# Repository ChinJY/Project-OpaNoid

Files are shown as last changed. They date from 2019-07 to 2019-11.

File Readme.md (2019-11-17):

## Project OpaNoid

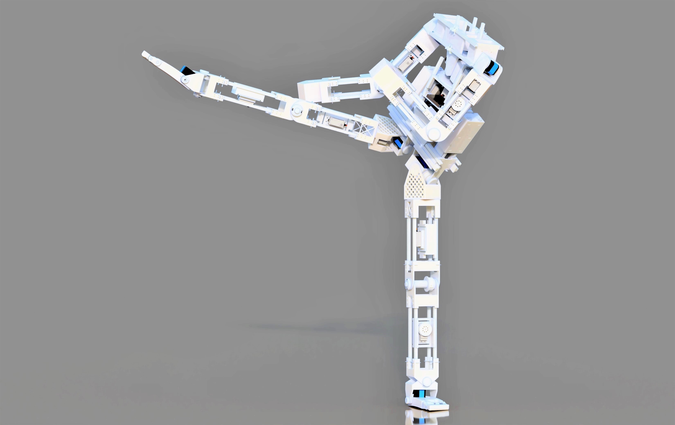
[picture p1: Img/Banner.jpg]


-   Project OpaNoid is an teen to adult-sized humanoid robot designed
    for education and research. It is highly modular
    and can be modified on the fly using only simple tools such as hex-head
    screwdrivers.

-   Its chassis has been designed to be completely printed with using FDM
    3D printing (the most accessible 3D printing technique at present)

-   By focusing on the humanoid form, greater attention can be paid to the key
    objectives of Project Opanoid; namely its variable mass distribution,
    variable dimensions, scalability (servos can be stacked to support higher
    torque requirements) and expandability (add-ons such as sensors can be added
    without modification to the core structure through the use of
    rail-mountings)

### Open Source

Project OpaNoid is open source under Creative Commons BY-SA 4.0 for hardware and GNU GPL v3 for software.

### Getting started

-   [Bill of materials](Hardware/Bill%20of%20materials.pdf)

-   [Printing guidelines](Hardware/Print%20settings.md)

-   [Software setup](Software/Software%20readme.md)

-   [Contribution Guidelines](Contributor%20guidelines.md)

-   [Codes of conduct](Codes%20of%20conduct.md)

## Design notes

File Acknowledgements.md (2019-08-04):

3216HTG servo: <https://grabcad.com/library/ars-3216htg-hv-1>

Turnigy S901D: <https://grabcad.com/library/turnigy-tgy-s901d-digital-servo-1>

9-axis imu:  <https://grabcad.com/library/adafruit-9-dof-imu-breakout-1>

pi camera: 
<https://grabcad.com/library/raspberry-pi-camera-module-v2-1/details?folder_id=4151951>

ultrasonic rangefinder: 
<https://grabcad.com/library/ultrasonic-sensor-hc-sr04-1>

LiPo battery:  <https://grabcad.com/library/lipo-battery-1-1>

AX-12A:  <https://grabcad.com/library/servo-dynamixel-ax-12a-1>

CR-10S: 
<https://grabcad.com/library/modified-creality-cr-10s-s3-model-3d-printer-assembly-1>

DQN template:
<https://github.com/sezan92/self_balancing_robot>

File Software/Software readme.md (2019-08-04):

-   Refer to this page to install Pigpio on Raspberry
    Pi: <http://abyz.me.uk/rpi/pigpio/download.html>

-   Install VNC solution (e.g. VNC viewer)

-   *Generate motion capture logs using Kinect on PC*

    -   Install kinect
        sdk: <https://www.microsoft.com/en-us/download/details.aspx?id=44561>

    -   Open ```BodyBasics-WPF.sln``` in Microsoft Visual Studio and run it
    
    -   Copy and paste the console output into an empty plain text file
    
    -   Delete all non-numerical items from the output in the beginning and the end, and save it as a text file to generate the motion capture log

        -   Please note that toe motions are not supported by
            kinect, so an additional capture device would be required
    
    -   Copy the motion capture log into ```Software/project_opanoid/walk_data```

-   *Controller program on raspberry pi*

    -   Save ```Software/Raspberry Pi/Opanoid_controller.c``` into your robot's Raspberry Pi 

    -   On your Raspberry Pi, copy the desired motion capture logs from ```Software/project_opanoid/walk_data``` to the same folder as the controller program

    -   Replace the path in line 29 of the controller program to the that of the motion capture log

    -   Run the controller program to make OpaNoid move in accordance with the motion capture log
    
-   *ROS package*

    -   Copy the ```project_opanoid``` folder into the source folder of your ROS workspace
        
    -   In Terminal, cd to your ROS workspace
    
    -   Type ```source devel/setup.bash``` (source the workspace)
    
    -   Enter different commands to open various functions:
    
        -   ```roslaunch project_opanoid display.launch``` to view the model of OpaNoid in Rviz
        
        -   ```roslaunch project_opanoid world.launch``` to view the model of OpaNoid in a Gazebo simulation
        
             -   Open another tab, go to the root folder of your ROS workspace,  source it and type ```rosrun project_opanoid_project_opanoid_node``` to move the robot using motion capture logs located in the Software/project_opanoid/walk_data folder
             
                 -   Change the file path in ```Software/project_opanoid/src/walk.cpp```, line 15 to that of your movement log in order to play it
                 
        -   ```roslaunch project_opanoid main_DQN.launch``` to make OpaNoid walk in Gazebo using a Deep Q Network Controller (not working at the moment)
    
    -   You can alter the simulated robot robot at ```Software/project_opanoid/urdf/opanoid_full.urdf```

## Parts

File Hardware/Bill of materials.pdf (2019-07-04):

## Bill of materials

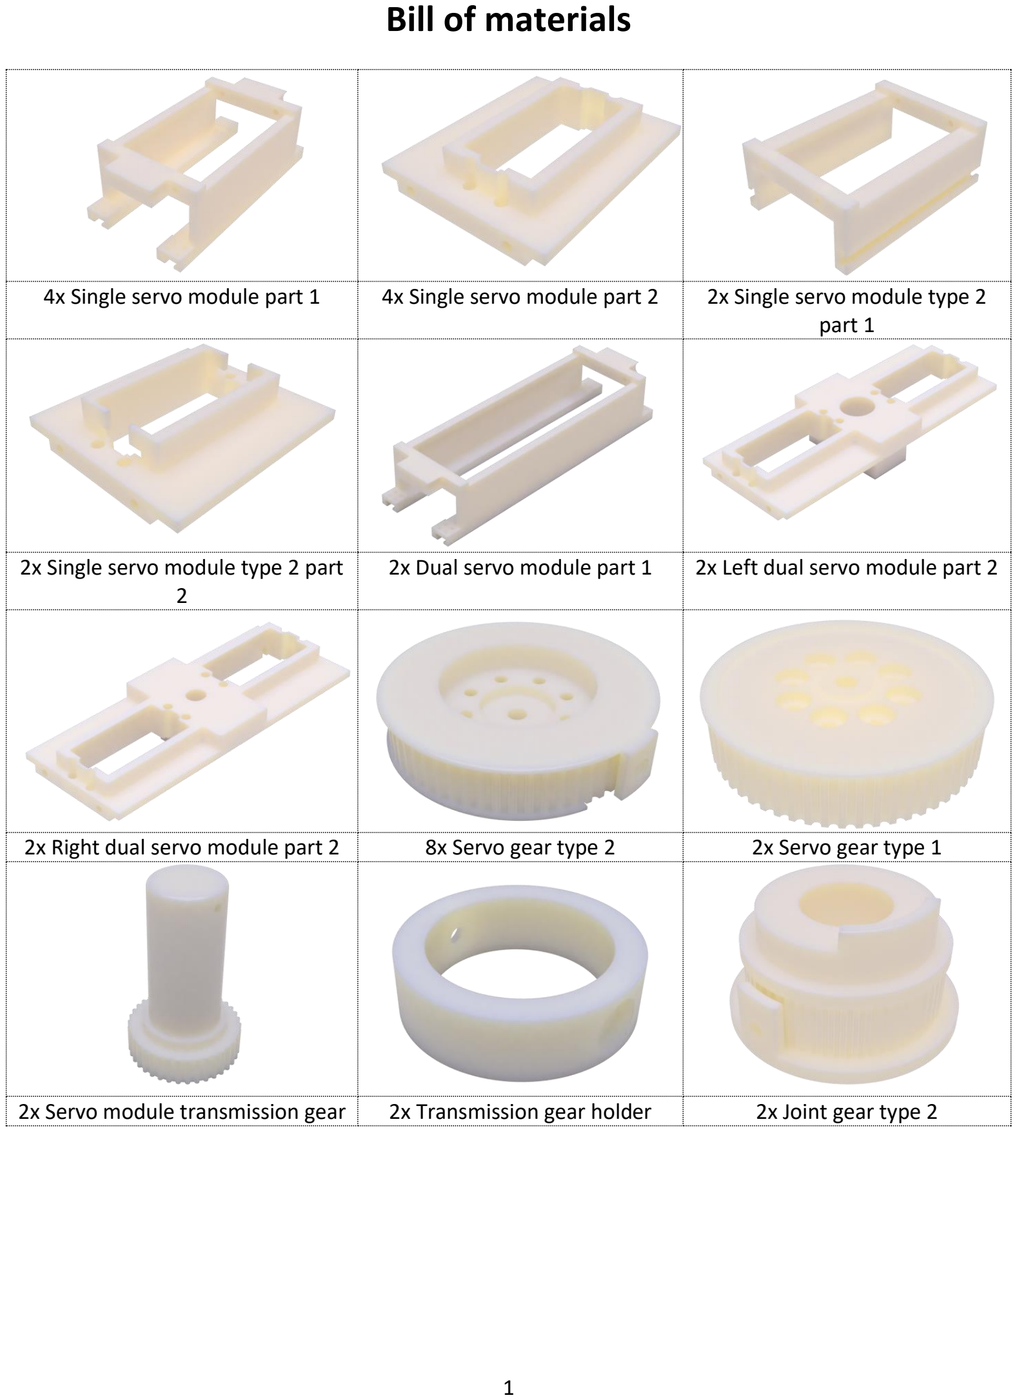
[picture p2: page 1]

4x Single servo module part 1 | 4x Single servo module part 2 | 2x Single servo module type 2 part 1

2x Single servo module type 2 part 2

2x Dual servo module part 1 | 2x Left dual servo module part 2
2x Right dual servo module part 2 | 8x Servo gear type 2 | 2x Servo gear type 1
2x Servo module transmission gear | 2x Transmission gear holder | 2x Joint gear type 2

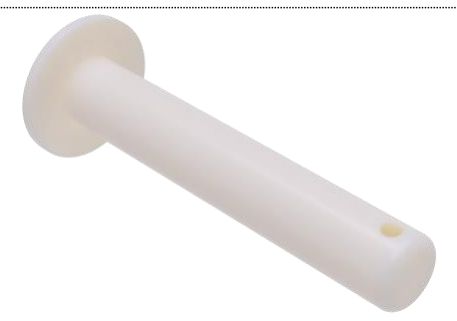
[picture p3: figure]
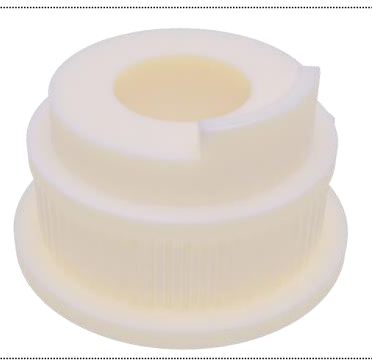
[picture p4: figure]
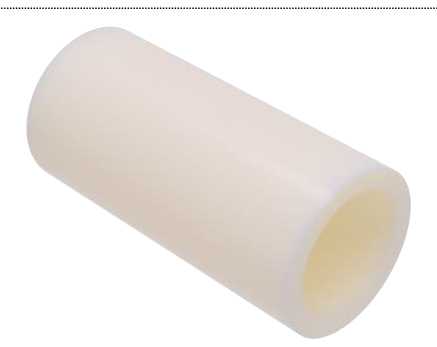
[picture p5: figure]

2x Joint gear type 2 | 4x Joint pin | 4x Joint spacer

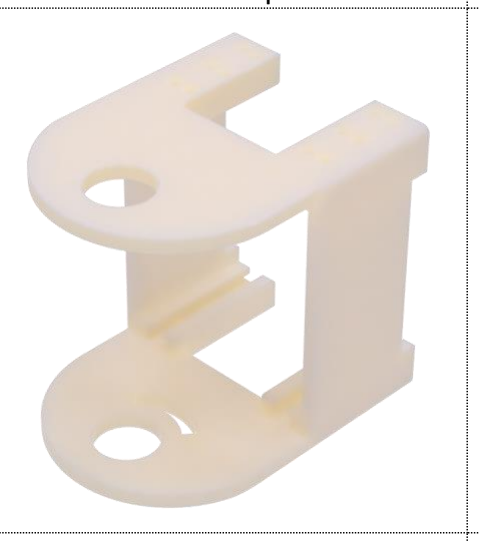
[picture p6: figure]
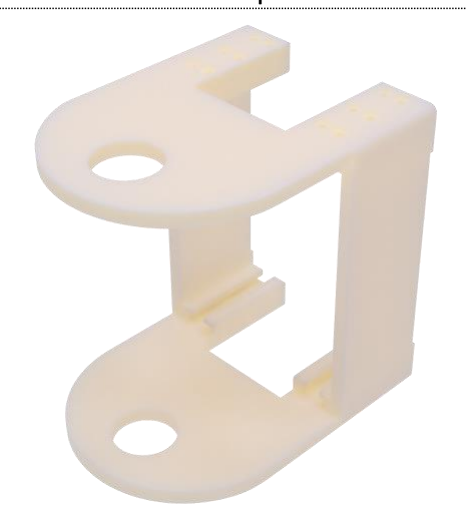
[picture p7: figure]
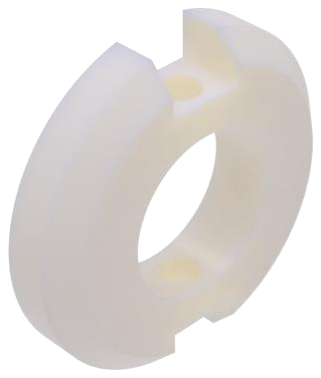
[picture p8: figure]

4x Joint holder | 4x Narrow Joint bracket | 4x Wide Joint bracket

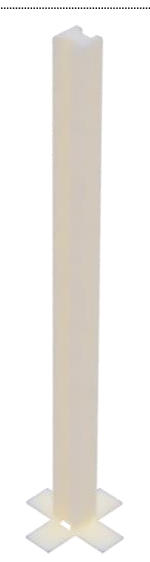
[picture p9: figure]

8x 140mm rail | 8x 160mm rail | 2x 250mm rail


4x 182.5mm rail | 4x 150mm rail | 4x 145mm rail


8x 132.5mm rail | 8x 112.5mm rail | 8x 115mm rail


2x pelvis rail | 1x Left pelvis gear | 1x Right pelvis gear


2x Pelvis bracket part 1 | 2x Pelvis bracket part 2 | 2x Outer pelvis pin
2x Outer pin holder | 2x Middle pelvis pin | 2x Rear pelvis pin
2x Rear pin holder | 1x Left pelvis attachment point | 1x Right pelvis attachment point
2x Rotation component | 1x Left ankle bracket part 1 | 1x Right ankle bracket part 1


2x Ankle bracket part 2 | 2x Left ankle bracket part 3 | 2x Left ankle bracket part 4
2x Ankle gear | 2x Ankle pin holder | 2x Ankle pin
2x Ankle spacer | 1x Abdominal base | 1x Waist part 1
1x Waist part 2 | 1x Waist part 3 | 1x Waist pin


1x Waist holder | 1x Raspberry Pi mount | Horizontal mount
Vertical mount | Vertical mount | 2x Arm attachment point
2x Arm rotation component | 1x Chest base | 1x Chest piece
2x Shoulder part 1 | 2x Shoulder part 2 | 1x Upper body base


1x Left vertical rotation
component


1x Right vertical rotation component


1x Horizontal rotation plate part 1


2x Horizontal rotation plate part 2 | 18x Turnigy S901D | 9x Robostar SRS-3216HTG
| No specific image


1x Raspberry Pi 3 Model B+ | 2x 8.4V LiPo battery | 1x 400-point breadboard

No specific image


1x Powerbank | Male-Male, Female-Male jumper wires


## Bill of materials by component

Upper torso
- 1x Upper body base
- 1x Horizontal rotation plate part 1
- 2x Horizontal rotation plate part 2
- 1x Left vertical rotation component
- 1x Right vertical rotation component
- 1x Chest base
- 1x Chest piece
- 4x 145mm rail
- 8x 132.5mm rail
- 2x Shoulder part 1
- 2x Shoulder part 2

Right arm
- 4x 112.5mm rail
- 4x 115mm rail
- 1x Arm attachment point
- 1x Arm rotation component
- 1x Hand
- 1x Joint gear type 2
- 1x Joint pin holder
- 1x Joint pin
- 1x Joint spacer
- 1x Narrow joint bracket
- 1x Wide joint bracket
- 1x Single servo module part 1
- 1x Single servo module part 2
- 1x Servo gear type 2

Left arm
- 4x 112.5mm rail
- 4x 115mm rail
- 1x Arm attachment point
- 1x Arm rotation component
- 1x Hand
- 1x Joint gear type 1
- 1x Joint pin holder
- 1x Joint pin
- 1x Joint spacer
- 1x Narrow joint bracket
- 1x Wide joint bracket
- 1x Single servo module part 1

- 1x Single servo module part 2
- 1x Servo gear type 2

Pelvis
- 2x Dual servo module part 1
- 1x Left dual servo module part 2
- 1x Right dual servo module part 2
- 2x Servo gear type 2
- 2x Servo gear type 1
- 2x Servo module transmission gear
- 2x Transmission gear holder
- 2x Servo module stiffener
- 4x 182.5mm rail
- 2x 250mm rail
- 2x pelvis rail
- 2x Pelvis bracket part 1
- 2x Pelvis bracket part 2
- 2x Rear pelvis pin
- 2x Rear pin holder
- 2x Middle pelvis pin
- 2x Middle pin holder
- 2x Outer pelvis pin
- 2x Outer pin holder
- Left pelvis gear
- Right pelvis gear

Abdomen
- 1x Abdominal base
- 4x 150mm rail
- 1x Waist part 1
- 1x Waist part 2
- 1x Waist part 3
- 1x Waist pin holder
- 1x Waist pin
- 1x Raspberry Pi mount
- 3x combination of Vertical and Horizontal mounts
- Vertical mount part 2 (quantity as required)

Right leg
- 1x Right pelvis attachment bracket
- 1x Rotation component
- 4x 160mm rail
- 4x 140mm rail
- 1x Single servo module part 1

- 1x Single servo module part 2
- 1x Single servo module type 2 part 1
- 1x Single servo module type 2 part 2
- 1x Single servo module type 2 part 1
- 1x Single servo module type 2 part 2
- 2x Servo gear type 2
- 1x Wide joint bracket
- 1x Narrow joint bracket
- 1x Joint gear type 2
- 1x Joint pin
- 1x Joint spacer
- 1x Joint pin holder
- 1x Right ankle bracket part 1
- 1x Ankle bracket part 2
- 1x Ankle bracket part 3
- 1x Ankle bracket part 4
- 1x Ankle gear
- 1x Ankle pin
- 1x Ankle pin holder
- 1x Ankle spacer

Right Foot
- 1x Right foot part 1
- 1x Right foot part 2
- 1x Right foot part 3
- 1x Right foot part 4
- 1x Foot pin

Left leg
- 1x Left pelvis attachment bracket
- 1x Rotation component
- 4x 160mm rail
- 4x 140mm rail
- 1x Single servo module part 1
- 1x Single servo module part 2
- 1x Single servo module type 2 part 1
- 1x Single servo module type 2 part 2
- 1x Single servo module type 2 part 1
- 1x Single servo module type 2 part 2
- 2x Servo gear type 2
- 1x Wide joint bracket
- 1x Narrow joint bracket
- 1x Joint gear type 1
- 1x Joint pin

- 1x Joint spacer
- 1x Joint pin holder
- 1x Left ankle bracket part 1
- 1x Ankle bracket part 2
- 1x Ankle bracket part 3
- 1x Ankle bracket part 4
- 1x Ankle gear
- 1x Ankle pin
- 1x Ankle pin holder
- 1x Ankle spacer

Left Foot
- 1x Left foot part 1
- 1x Left foot part 2
- 1x Left foot part 3
- 1x Left foot part 4
- 1x Foot pin

Electronics
- 18x Turnigy S901D
- 9x Robostar SRS-3216HTG
- 2x Corona DS-239HV
- 1x Raspberry Pi 3 Model B+
- 2x 8.4V LiPo battery
- 1x 400-point breadboard
- 1x Powerbank
- Male-Male, Female-Male jumper wires

Image sources

RoboStar SRS-3216HTG: https://cdn-global-hk.hobbyking.com/media/catalog/product/cache/1/image/660x415/17f82f742ffe127f42dca9de82fb58b1/legacy/catalog/64644.jpg

Raspberry Pi 3 Model B+: https://www.raspberrypi.org/app/uploads/2018/03/770A5842-462x322.jpg

400-point breadboard:
https://www.robotshop.com/media/catalog/product/cache/image/900x900/9df78eab33525d08d6e5fb8d27136e95/4/0/400-tie-point-solderless-interlocking-breadboard_2.jpg (https://www.robotshop.com/media/catalog/product/cache/image/900x900/9df78eab33525d08d6e5fb8d27136e95/4/0/400-tie-point-solderless-interlocking-breadboard_2.jpg)

Jumper wires: https://www.digibay.in/image/cache/data/se/274-a-solderless-breadboard-prototyping-jumper-wires-male-to-male-600x600.jpg

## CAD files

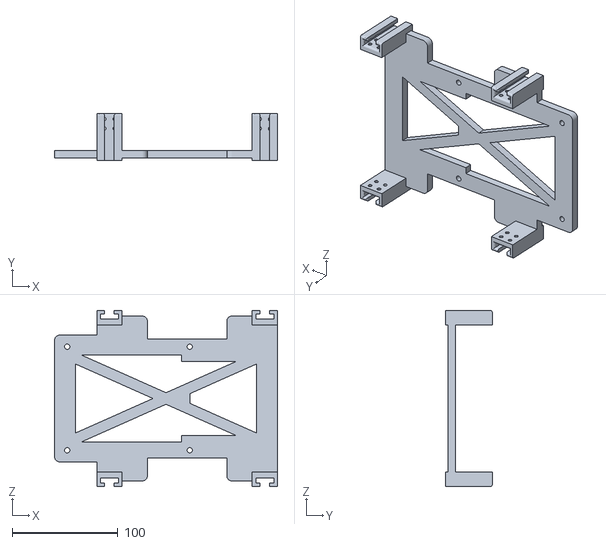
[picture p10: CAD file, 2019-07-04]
Hardware/STL files/Abdomen/Raspberry Pi mount.stl
211.0 x 44.0 x 167.0

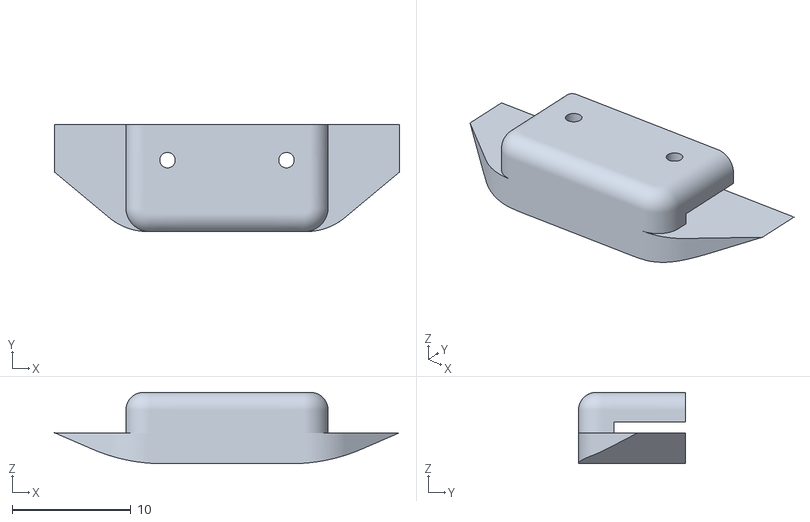
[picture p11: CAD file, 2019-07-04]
Hardware/STL files/Belt binder.stl
29.0 x 9.00 x 6.00

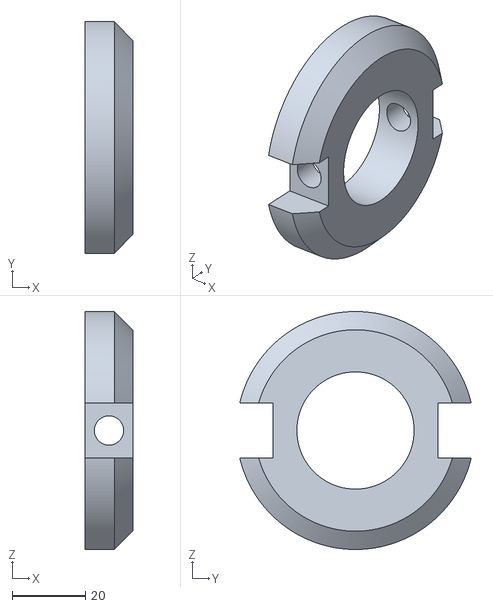
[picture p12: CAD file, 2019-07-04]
Hardware/STL files/Joint/Joint pin holder.stl
13.0 x 63.2 x 65.0

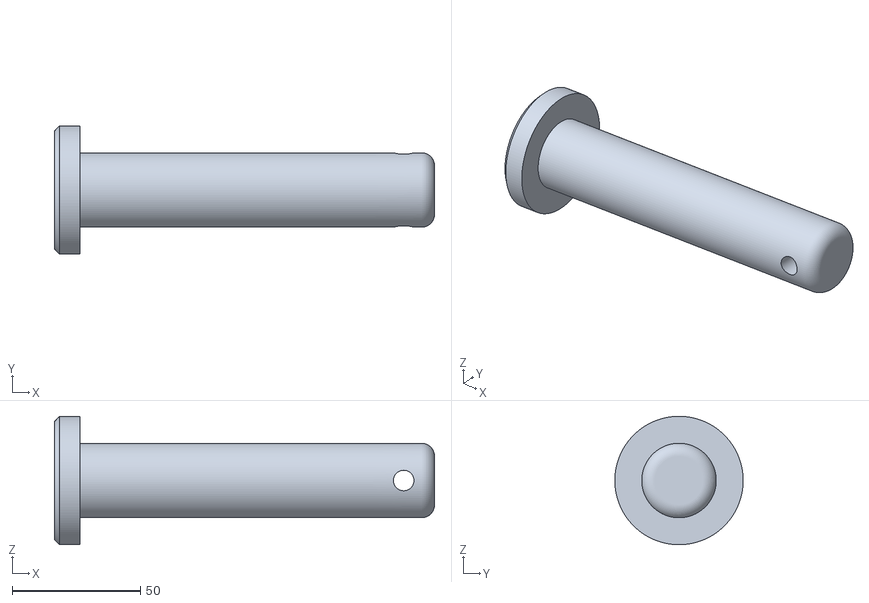
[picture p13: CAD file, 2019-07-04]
Hardware/STL files/Leg/Ankle/Ankle pin.stl
148.0 x 50.0 x 50.0

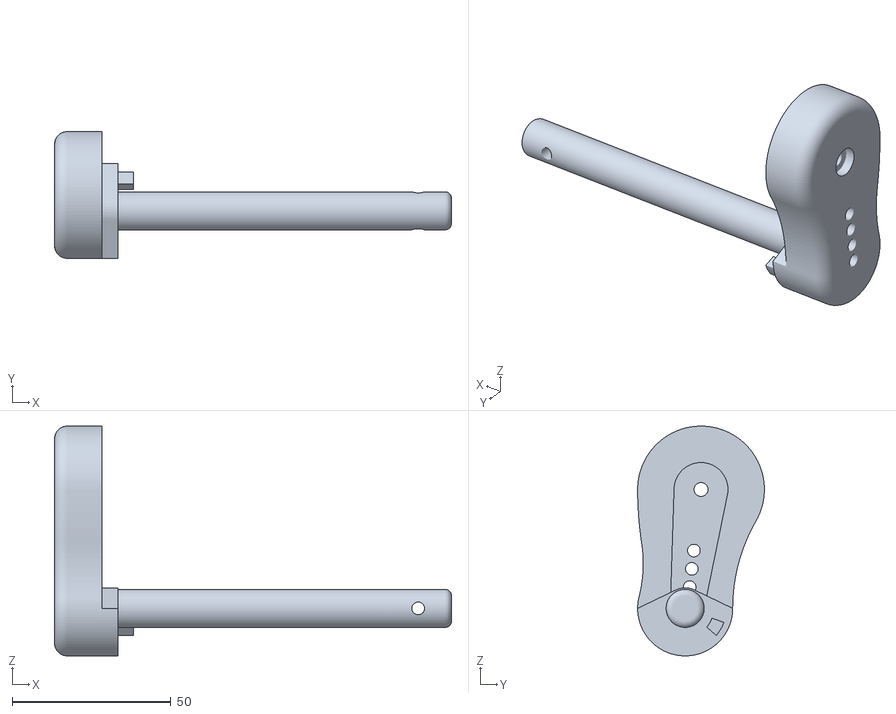
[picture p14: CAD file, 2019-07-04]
Hardware/STL files/Leg/Foot/Left foot part 2.stl
125.2 x 40.0 x 72.5

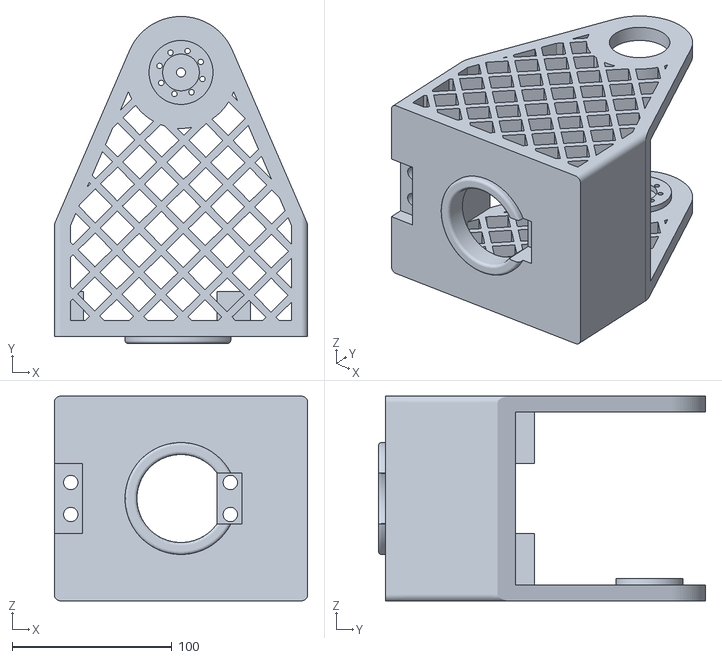
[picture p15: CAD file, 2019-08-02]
Hardware/STL files/Leg/Right pelvis attachment bracket.stl
158.5 x 204.5 x 128.0

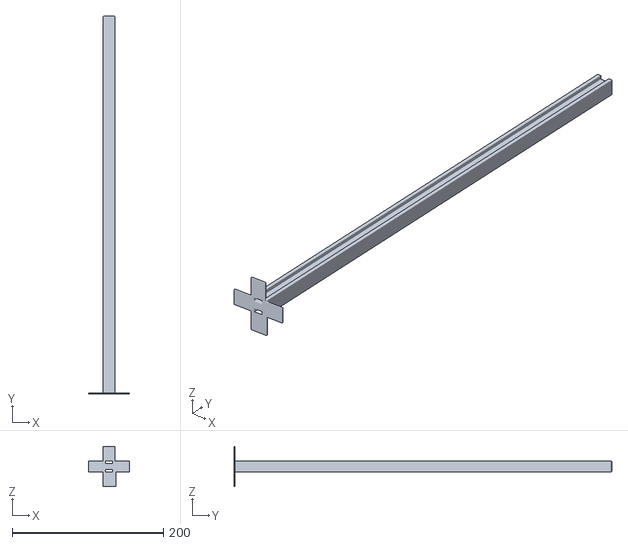
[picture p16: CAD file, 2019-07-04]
Hardware/STL files/Pelvis/250mm rail.stl
54.0 x 500.0 x 53.0

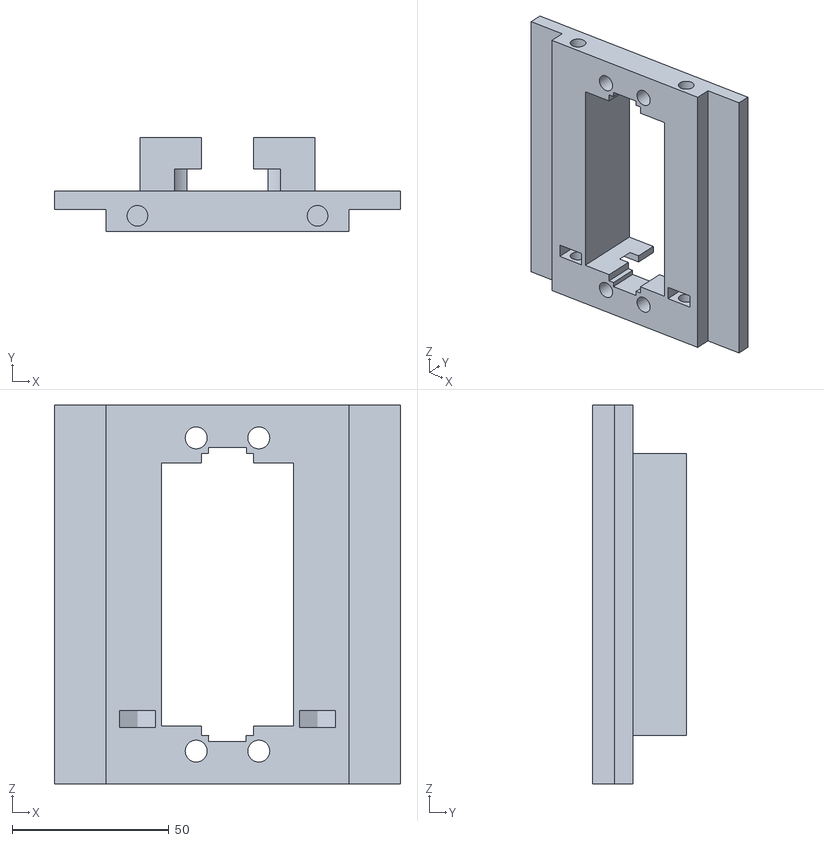
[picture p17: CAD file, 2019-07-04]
Hardware/STL files/Servo modules/Single servo module type 2 part 2.stl
110.5 x 30.0 x 121.0

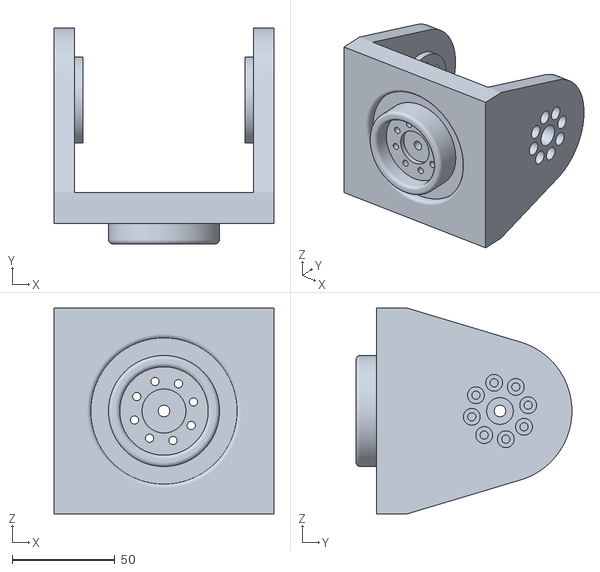
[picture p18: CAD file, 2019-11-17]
Hardware/STL files/Upper torso/Arm attachment point.stl
107.0 x 105.0 x 100.0

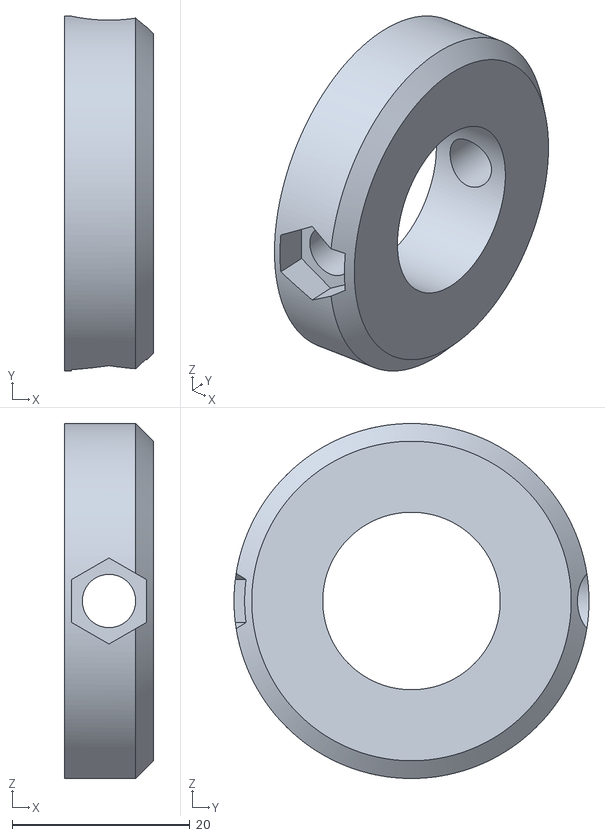
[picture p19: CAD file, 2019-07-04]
Hardware/STL files/Abdomen/Waist pin holder.stl
10.0 x 40.0 x 40.0

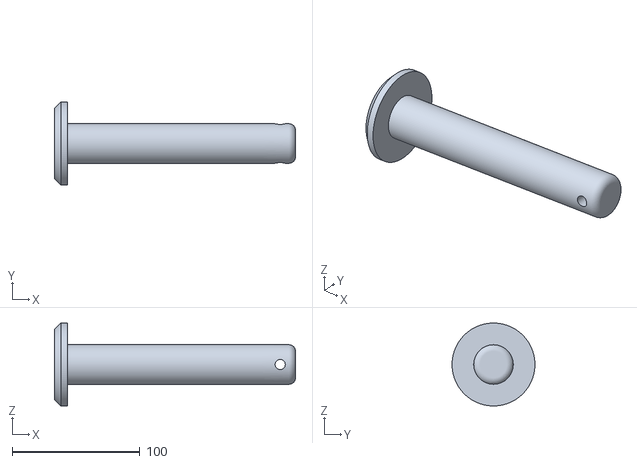
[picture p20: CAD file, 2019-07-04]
Hardware/STL files/Joint/Joint pin.stl
189.0 x 65.0 x 65.0

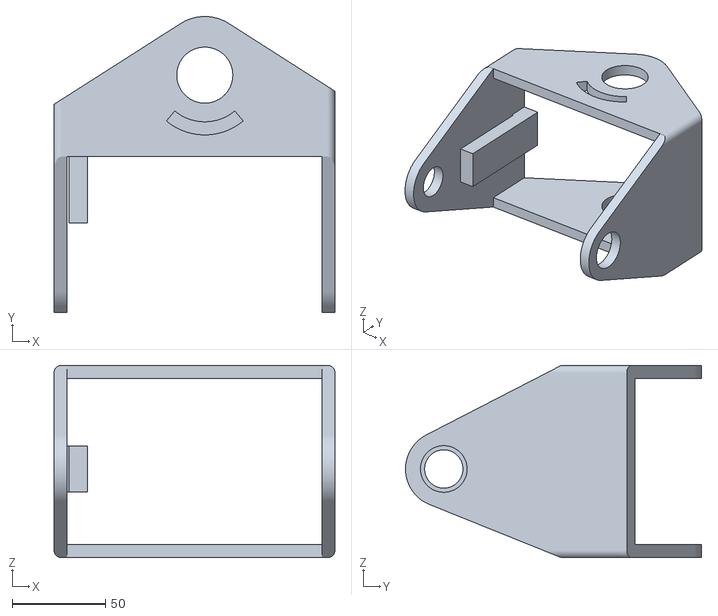
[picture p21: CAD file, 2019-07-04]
Hardware/STL files/Leg/Ankle/Left ankle bracket part 1.stl
150.4 x 158.5 x 103.0

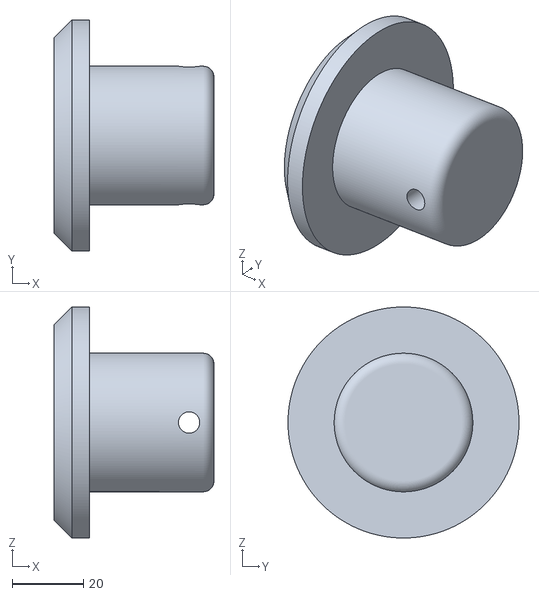
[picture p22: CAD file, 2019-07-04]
Hardware/STL files/Pelvis/Rear pelvis pin.stl
45.0 x 65.0 x 65.0

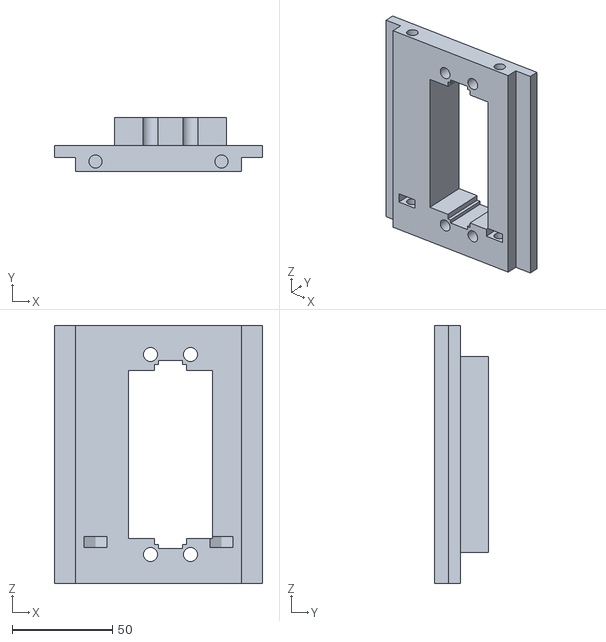
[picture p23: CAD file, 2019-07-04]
Hardware/STL files/Servo modules/Single servo module type 1 part 2.stl
104.0 x 27.0 x 129.0

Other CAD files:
Hardware/STL files/Leg/Foot/RIght foot part 2.stl
Hardware/STL files/Leg/Left pelvis attachment bracket.stl
Hardware/STL files/Upper torso/Shoulder part 2.stl
Hardware/STL files/Abdomen/Waist part 2.stl
Hardware/STL files/Abdomen/150mm rail.stl
Hardware/STL files/Abdomen/Abdominal base.stl
Hardware/STL files/Abdomen/Horizontal mount part 2.stl
Hardware/STL files/Abdomen/Horizontal mount.stl
Hardware/STL files/Abdomen/Vertical mount part 2.stl
Hardware/STL files/Abdomen/Vertical mount.stl
Hardware/STL files/Abdomen/Waist part 1.stl
Hardware/STL files/Abdomen/Waist part 3.stl
Hardware/STL files/Abdomen/Waist pin.stl
Hardware/STL files/Joint/Joint pin.f3d
Hardware/STL files/Joint/Joint spacer.stl
Hardware/STL files/Joint/Narrow joint bracket.stl
Hardware/STL files/Joint/Wide joint bracket.stl
Hardware/STL files/Leg/140mm rail.stl
Hardware/STL files/Leg/160mm rail.stl
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

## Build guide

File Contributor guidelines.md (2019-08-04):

Thank you for contributing to Project OpaNoid! The following is a set
of guidelines for contributing to Project
OpaNoid. Above all, these are guidelines, not rules. Use your
best judgement, and feel free to propose changes to this document through
a pull request. 

## Getting started

### Design Considerations of Project OpaNoid

These design considerations serve as guidelines to increase the ease with which you can integrate your hardware contributions with the project, and are by no means supposed to be definitive.

### Design Ideology (as stated in Readme)

-   By focusing on the humanoid form, greater attention can be paid to the key
    objectives of Project Opanoid; namely its variable mass distribution,
    variable dimensions, scalability (servos can be stacked to support higher
    torque requirements) and expandability (add-ons such as sensors can be added
    without modification to the core structure through the use of rail
    mountings)

### Designing for FDM printing

-   Certain parts have had a portion of their bases raised to facilitate removal
    from the build plate

-   Parts are shaped such that support material required to print them is
    minimised

-   All rail guides along with most joints/pins are designed to be printed
    vertically to increase accuracy

-   Tolerances are mostly rather generous to take into account 3D printers that
    are unable to achieve high levels of refinement

-   Parts are are composed of flat surfaces to reduce printing time, with the
    exception of areas where contouring would be functional, such as the feet

-   Parts are engineered with the material limits of 3D printed PLA in mind

-   Certain parts with very small bases (e.g. the rails) have flaps on the
    bottom in order to increase base area for better adhesion to the build
    plate-these flaps can be broken off the main part relatively cleanly without
    the use of tools

-   As far as possible, parts are designed to be symmetrical along the vertical
    and horizontal axes in order to increase reusability and avoid waste
    materials and time (you don't want to spend hours printing a part for the
    left knee only to realise it was the right knee that needed the part!)

### Functional Considerations

-   Parts are designed to be "open" to increase accessibility during assembly
    and minimise mass

-   With the exception of certain areas, most screws are designed to be used
    without nuts-the threads created by the screw in the plastic through
    self-taping is sufficient to hold the screw in place

-   Brackets are designed such that the rails can extend through most of their
    length, enabling the mounting brackets to be positioned along the rails with
    fewer restrictions

-   The thickness of the part walls are minimised (taking into consideration the
    frailties of the construction material) in order to minimise mass, such that
    the robot's frame constitutes as small a component of the overall mass as
    possible

    -   This would allow the mass distribution of the robot to be controlled
        with greater authority through the positioning of servos and electronics
        within the frame

### Hardware documentation 

-   Please refer to ```Hardware/Schematics``` for schematics of the
    OpaRail system and rail spacings within the limbs and torso 

### How do I contribute?

#### Hardware

-   Due to the modularity of Project OpaNoid, it is possible to add new ideas
    without overriding existing ones

-   Since we would like to encourage variety, we
    prefer not to delete existing ideas (they may have elements which
    we can still learn from!)

-   Hence, contributors are encouraged to add to, rather than replace existing
    material

-   If you intend to override an existing file with a new one, please
    refrain from deleting it in your fork. Instead, append your contribution
    to the existing project as per the default procedure but mention the
    file you wish to replace in the pull request, and we
    will review your request 

    -   We may decide to add your contribution but preserve the file you wish to replace 

#### Software

-   The software for Project OpaNoid is at a
    lower developmental state than the hardware. As such, contributions to flesh
    out the software, in particular the controller, are most welcome.

-   Create a pull request with a general description of your modifications, and
    we will review your contribution

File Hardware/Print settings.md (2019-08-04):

These are settings that were found to provide sufficient material strength for
the parts while maintaining a relatively print time. You may choose to follow
your own settings, especially if you are using a different material.

**Material:** eSun Pla+ (density 1.24gcm-3)

**Nozzle diameter:** 0.4mm

**Layer height:**

-   0.1mm for gears 

-   0.2mm for all other parts

**Infill:** gyroid/grid for all except gears, concentric for gears

**Wall width:** 1.6mm

**Density:**

-   100% for rails directly attached to servo mounts and gears

-   50% for horizontal rotation plate

-   5% for hands

-   20% for all other parts 

**Print Orientation:**

-   Horizontal: gears

-   Vertical: all other parts

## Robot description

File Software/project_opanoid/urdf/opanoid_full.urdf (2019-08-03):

<?xml version="1.0"?>
<robot name="Opanoid_sketch">

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
  <link name="base_link">
  	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
		<inertial>
      <mass value="0.272"/>
      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
    </inertial>
	</link>
	<link name="pelvis_lower">
  	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
		<inertial>
      <mass value="0.078"/>
      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
    </inertial>
	</link>
	<link name="servo_mounts">
  	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
		<inertial>
      <mass value="0.672"/>
      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
    </inertial>
	</link>
	<link name="l_pelvis_bracket_2">
  	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
		<inertial>
      <mass value="0.11"/>
      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
    </inertial>
  </link>
  <link name="r_pelvis_bracket_2">
  	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
		<inertial>
      <mass value="0.11"/>
      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
    </inertial>
  </link>
  
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
	<link name="l_pelvis_attachment">
  	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
		<inertial>
      <mass value="0.174"/>
      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
    </inertial>
  </link>
  <link name="l_140mm_rail">
  	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
		<inertial>
      <mass value="0.03"/>
      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
    </inertial>
  </link>
  <link name="l_servo_module_t1">
  	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
		<inertial>
      <mass value="0.118"/>
      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
    </inertial>
  </link>
  <link name="l_u_knee_joint">
  	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
		<inertial>
      <mass value="0.048"/>
      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
    </inertial>
  </link>
  <link name="l_joint_hinge">
  	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
		<inertial>
      <mass value="0.045"/>
      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
    </inertial>
  </link>
  <link name="l_l_knee_joint">
  	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
		<inertial>
      <mass value="0.05"/>
      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
    </inertial>
  </link>
  <link name="l_160mm_rail">
  	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
		<inertial>
      <mass value="0.035"/>
      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
    </inertial>
  </link>
  <link name="l_servo_module_t2">
  	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
		<inertial>
      <mass value="0.105"/>
      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
    </inertial>
  </link>
	<link name="l_ankle_2">
  	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
		<inertial>
      <mass value="0.073"/>
      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
    </inertial>
  </link>
  <link name="l_ankle_1">
  	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
		<inertial>
      <mass value="0.036"/>
      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
    </inertial>
  </link>
  <link name="leftFoot">
  	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
		<inertial>
      <mass value="0.146"/>
      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
    </inertial>
  </link>
  <link name="leftToe">
  	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
		<inertial>
      <mass value="0.42"/>
      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
    </inertial>
  </link>

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
  <link name="r_pelvis_attachment">
  	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
		<inertial>
      <mass value="0.174"/>
      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
    </inertial>
  </link>
  <link name="r_140mm_rail">
  	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
		<inertial>
      <mass value="0.03"/>
      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
    </inertial>
  </link>
  <link name="r_servo_module_t1">
  	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
		<inertial>
      <mass value="0.118"/>
      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
    </inertial>
  </link>
  <link name="r_u_knee_joint">
  	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
		<inertial>
      <mass value="0.048"/>
      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
    </inertial>
  </link>
  <link name="r_joint_hinge">
  	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
		<inertial>
      <mass value="0.045"/>
      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
    </inertial>
  </link>
  <link name="r_l_knee_joint">
  	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
		<inertial>
      <mass value="0.05"/>
      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
    </inertial>
  </link>
  <link name="r_160mm_rail">
  	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
		<inertial>
      <mass value="0.035"/>
      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
    </inertial>
  </link>
  <link name="r_servo_module_t2">
  	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
		<inertial>
      <mass value="0.105"/>
      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
    </inertial>
  </link>
  <link name="r_ankle_2">
  	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
		<inertial>
      <mass value="0.073"/>
      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
    </inertial>
  </link>
  <link name="r_ankle_1">
  	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
		<inertial>
      <mass value="10"/>
      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
    </inertial>
  </link>
  <link name="rightFoot">
  	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
		<inertial>
      <mass value="0.146"/>
      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
    </inertial>
  </link>
  <link name="rightToe">
  	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
		<inertial>
      <mass value="0.42"/>
      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
    </inertial>
  </link>
  <link name="imu_link">
  	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
    <inertial>
      <mass value="1e-5" />
      <origin xyz="0 0 0" rpy="0 0 0"/>
      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
    </inertial>
  </link>

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
	<joint name="pelvis_internal" type="fixed">
    <parent link="base_link"/>
    <child link="pelvis_lower"/>
		<origin xyz="0 0 -0.0325" rpy="0 0 0"/>
  </joint>
  
  <joint name="pelvis_servo" type="fixed">
    <parent link="base_link"/>
    <child link="servo_mounts"/>
		<origin xyz="0 0 0.05" rpy="0 0 0"/>
  </joint>
  
	<joint name="leftThighY" type="revolute">
    <parent link="pelvis_lower"/>
    <child link="l_pelvis_bracket_2"/>
    <axis xyz="0 -1 0"/>
    <limit effort="100.0" lower="-1.570" upper="1.570" velocity="7.48"/>
		<origin xyz="0 0.0385 -0.015" rpy="0 0 0"/>
  </joint>
  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
  
  <joint name="leftThighX" type="revolute">
    <parent link="l_pelvis_bracket_2"/>
    <child link="l_pelvis_attachment"/>
    <axis xyz="1 0 0"/>
    <limit effort="100.0" lower="-0.15" upper="1.570" velocity="6.546"/>
		<origin xyz="0 0.007 0" rpy="0 0 0"/>
  </joint>
  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
  
  <joint name="l_upper_thigh" type="fixed">
    <parent link="l_pelvis_attachment"/>
    <child link="l_140mm_rail"/>
		<origin xyz="0 0 -0.1" rpy="0 0 0"/>
  </joint>
  
  <joint name="l_lower_thigh" type="fixed">
    <parent link="l_140mm_rail"/>
    <child link="l_u_knee_joint"/>
		<origin xyz="0 0 -0.18" rpy="0 0 0"/>
  </joint>
  
  <joint name="l_kneeServo" type="fixed">
    <parent link="l_140mm_rail"/>
    <child link="l_servo_module_t1"/>
		<origin xyz="0 0 -0.09" rpy="0 0 0"/>
  </joint>  
  
  <joint name="l_hinge" type="fixed">
    <parent link="l_u_knee_joint"/>
    <child link="l_joint_hinge"/>
		<origin xyz="0 0 0" rpy="0 0 0"/>
  </joint>  
  
	<joint name="leftKnee" type="revolute">
    <parent link="l_u_knee_joint"/>
    <child link="l_l_knee_joint"/>
    <axis xyz="0 1 0"/>
    <limit effort="100.0" lower="0" upper="1.570" velocity="7.48"/>
		<origin xyz="0 0 0" rpy="0 0 0"/>
  </joint>
  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
  
  <joint name="l_upper_calf" type="fixed">
    <parent link="l_l_knee_joint"/>
    <child link="l_160mm_rail"/>
		<origin xyz="0 0 -0.05" rpy="0 0 0"/>
  </joint>
  
  <joint name="leftCalf" type="fixed">
    <parent link="l_160mm_rail"/>
    <child link="l_ankle_2"/>
    <axis xyz="0 1 0"/>
    <limit effort="100.0" lower="0" upper="1.570" velocity="7.48"/>
		<origin xyz="0 0 -0.15" rpy="0 0 0"/>
  </joint>
  
  <joint name="l_ankleServo" type="fixed">
    <parent link="l_160mm_rail"/>
    <child link="l_servo_module_t2"/>
		<origin xyz="0 0 -0.075" rpy="0 0 0"/>
  </joint> 
  
  <joint name="leftAnkleX" type="revolute">
    <parent link="l_ankle_2"/>
    <child link="l_ankle_1"/>
    <axis xyz="1 0 0"/>
    <limit effort="100.0" lower="-1.570" upper="1.570" velocity="7.48"/>
		<origin xyz="0 0 -0.04625" rpy="0 0 0"/>
  </joint>
  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
  
  <joint name="leftAnkleY" type="revolute">
    <parent link="l_ankle_1"/>
    <child link="leftFoot"/>
    <axis xyz="0 1 0"/>
    <limit effort="100.0" lower="-1.570" upper="1.570" velocity="7.48"/>
		<origin xyz="0 0 -0.07895" rpy="0 0 0"/>
  </joint>
  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
   
  <joint name="leftToe" type="revolute">
    <parent link="leftFoot"/>
    <child link="leftToe"/>
    <axis xyz="0 1 0"/>
    <limit effort="100.0" lower="-1.570" upper="1.570" velocity="7.48"/>
		<origin xyz="0.08545 0 -0.005" rpy="0 0 0"/>
  </joint>
  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
  
  <joint name="rightThighY" type="revolute">
    <parent link="pelvis_lower"/>
    <child link="r_pelvis_bracket_2"/>
    <axis xyz="0 -1 0"/>
    <limit effort="1000.0" lower="-1.570" upper="1.570" velocity="7.48"/>
		<origin xyz="0 -0.0385 -0.015" rpy="0 0 0"/>
  </joint>
  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
  
  <joint name="rightThighX" type="revolute">
    <parent link="r_pelvis_bracket_2"/>
    <child link="r_pelvis_attachment"/>
    <axis xyz="-1 0 0"/>
    <limit effort="100.0" lower="-0.15" upper="1.5705" velocity="6.546"/>
		<origin xyz="0 -0.007 0" rpy="0 0 0"/>
  </joint>
  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
  
  <joint name="r_upper_thigh" type="fixed">
    <parent link="r_pelvis_attachment"/>
    <child link="r_140mm_rail"/>
		<origin xyz="0 0 -0.1" rpy="0 0 0"/>
  </joint>
  
  <joint name="r_lower_thigh" type="fixed">
    <parent link="r_140mm_rail"/>
    <child link="r_u_knee_joint"/>
		<origin xyz="0 0 -0.18" rpy="0 0 0"/>
  </joint>
  
  <joint name="r_kneeServo" type="fixed">
    <parent link="r_140mm_rail"/>
    <child link="r_servo_module_t1"/>
		<origin xyz="0 0 -0.09" rpy="0 0 0"/>
  </joint>
  
  <joint name="r_hinge" type="fixed">
    <parent link="r_u_knee_joint"/>
    <child link="r_joint_hinge"/>
		<origin xyz="0 0 0" rpy="0 0 0"/>
  </joint>
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

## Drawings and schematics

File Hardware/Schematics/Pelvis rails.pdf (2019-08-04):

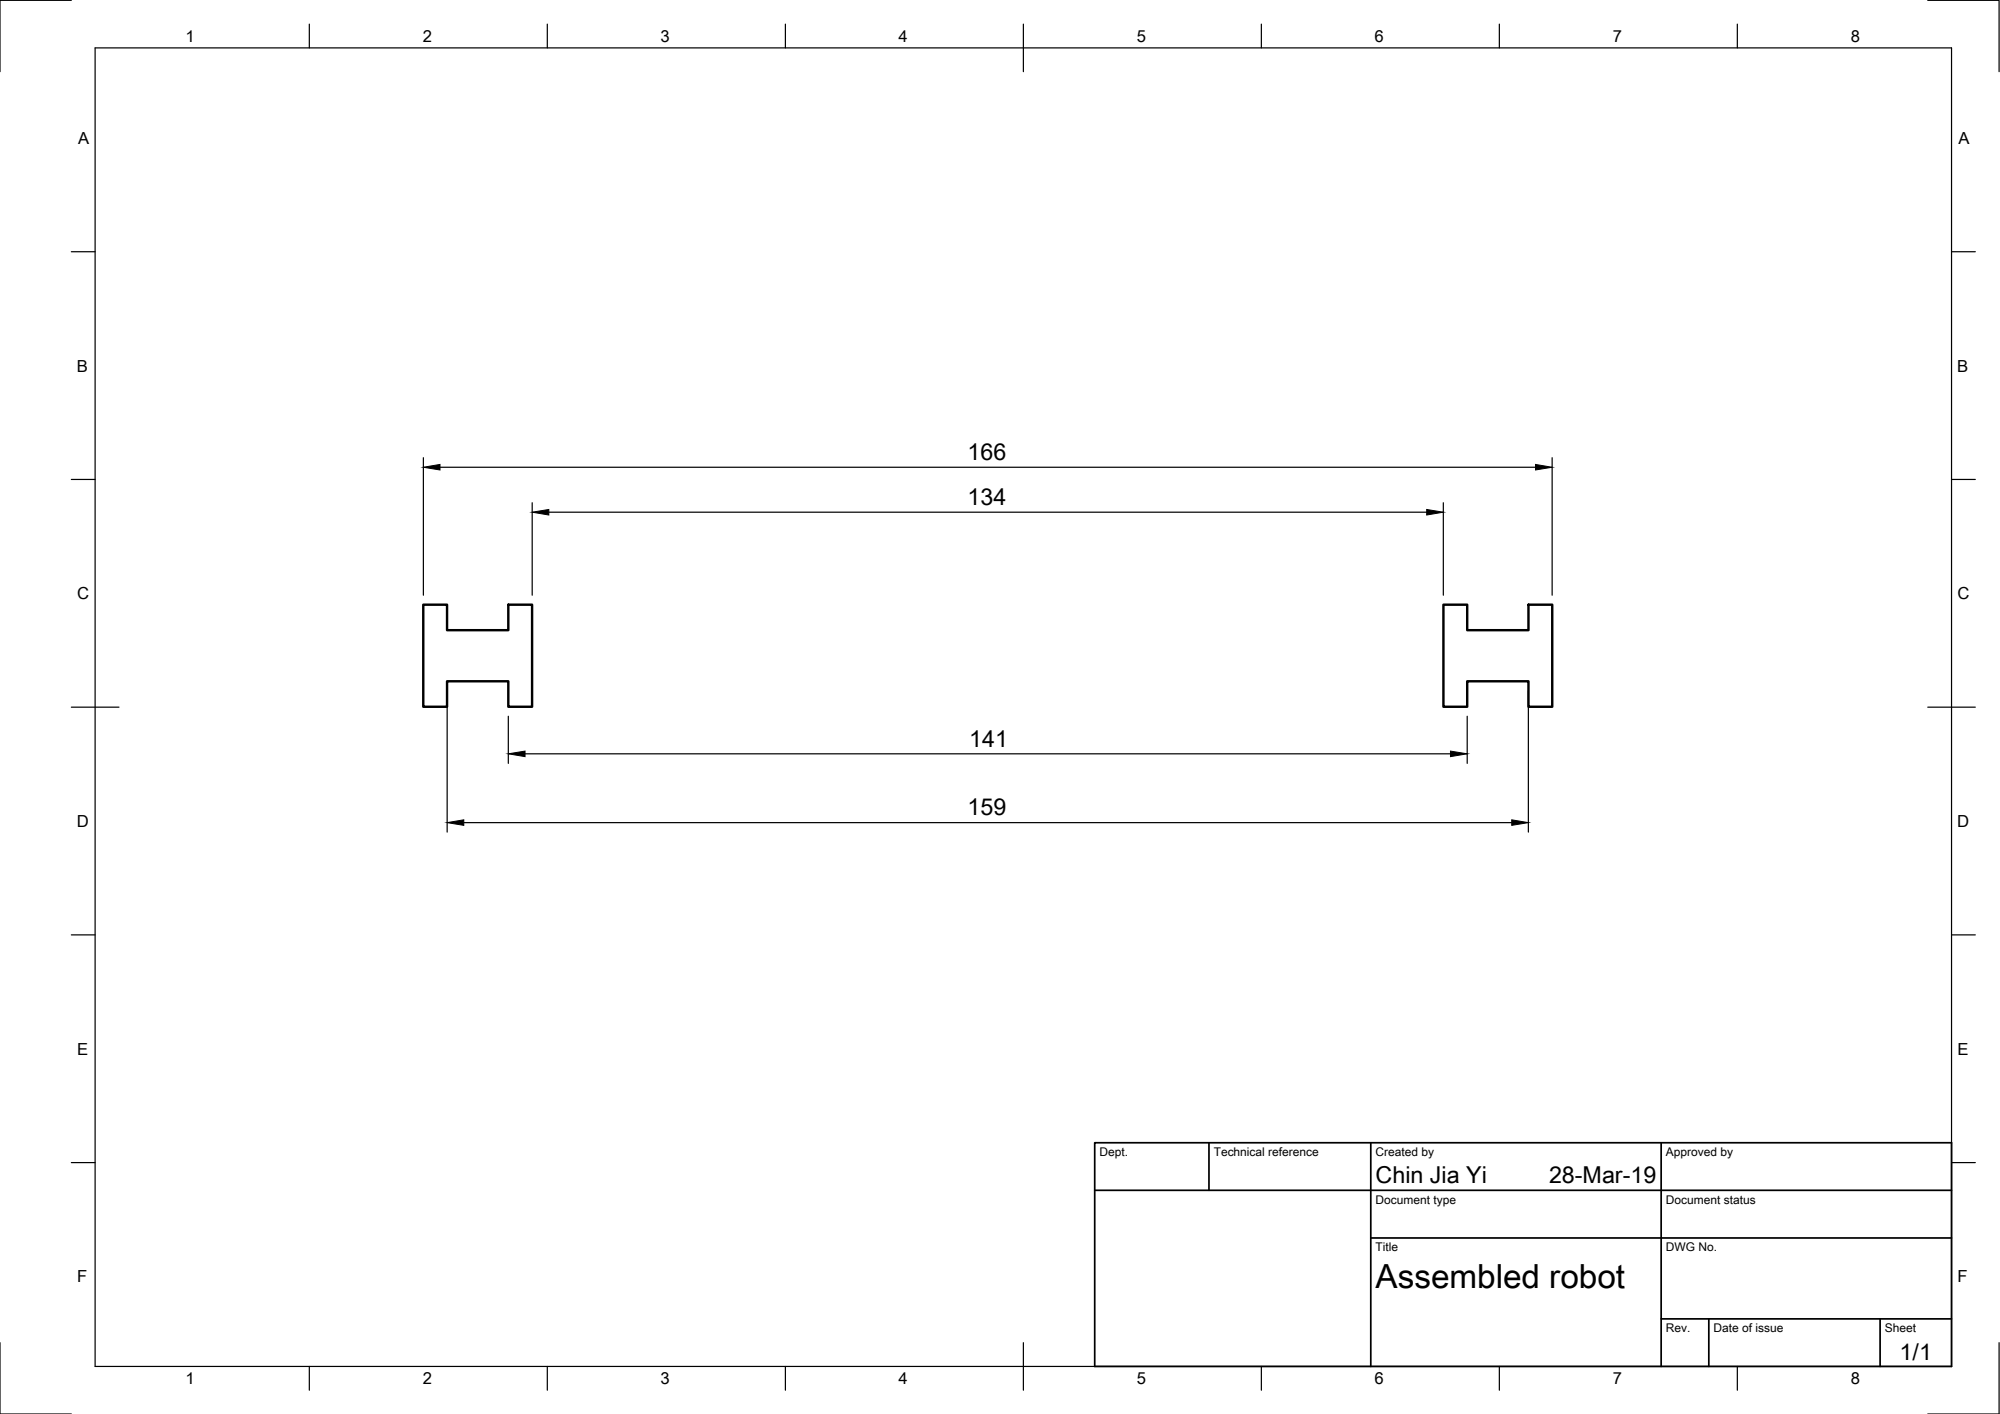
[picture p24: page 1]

Dept. | Technical reference | Created by Chin Jia Yi 28-Mar-19 | Approved by

Document type | Document status

Title Assembled robot | DWG No.

Rev. | Date of issue | Sheet 1/1

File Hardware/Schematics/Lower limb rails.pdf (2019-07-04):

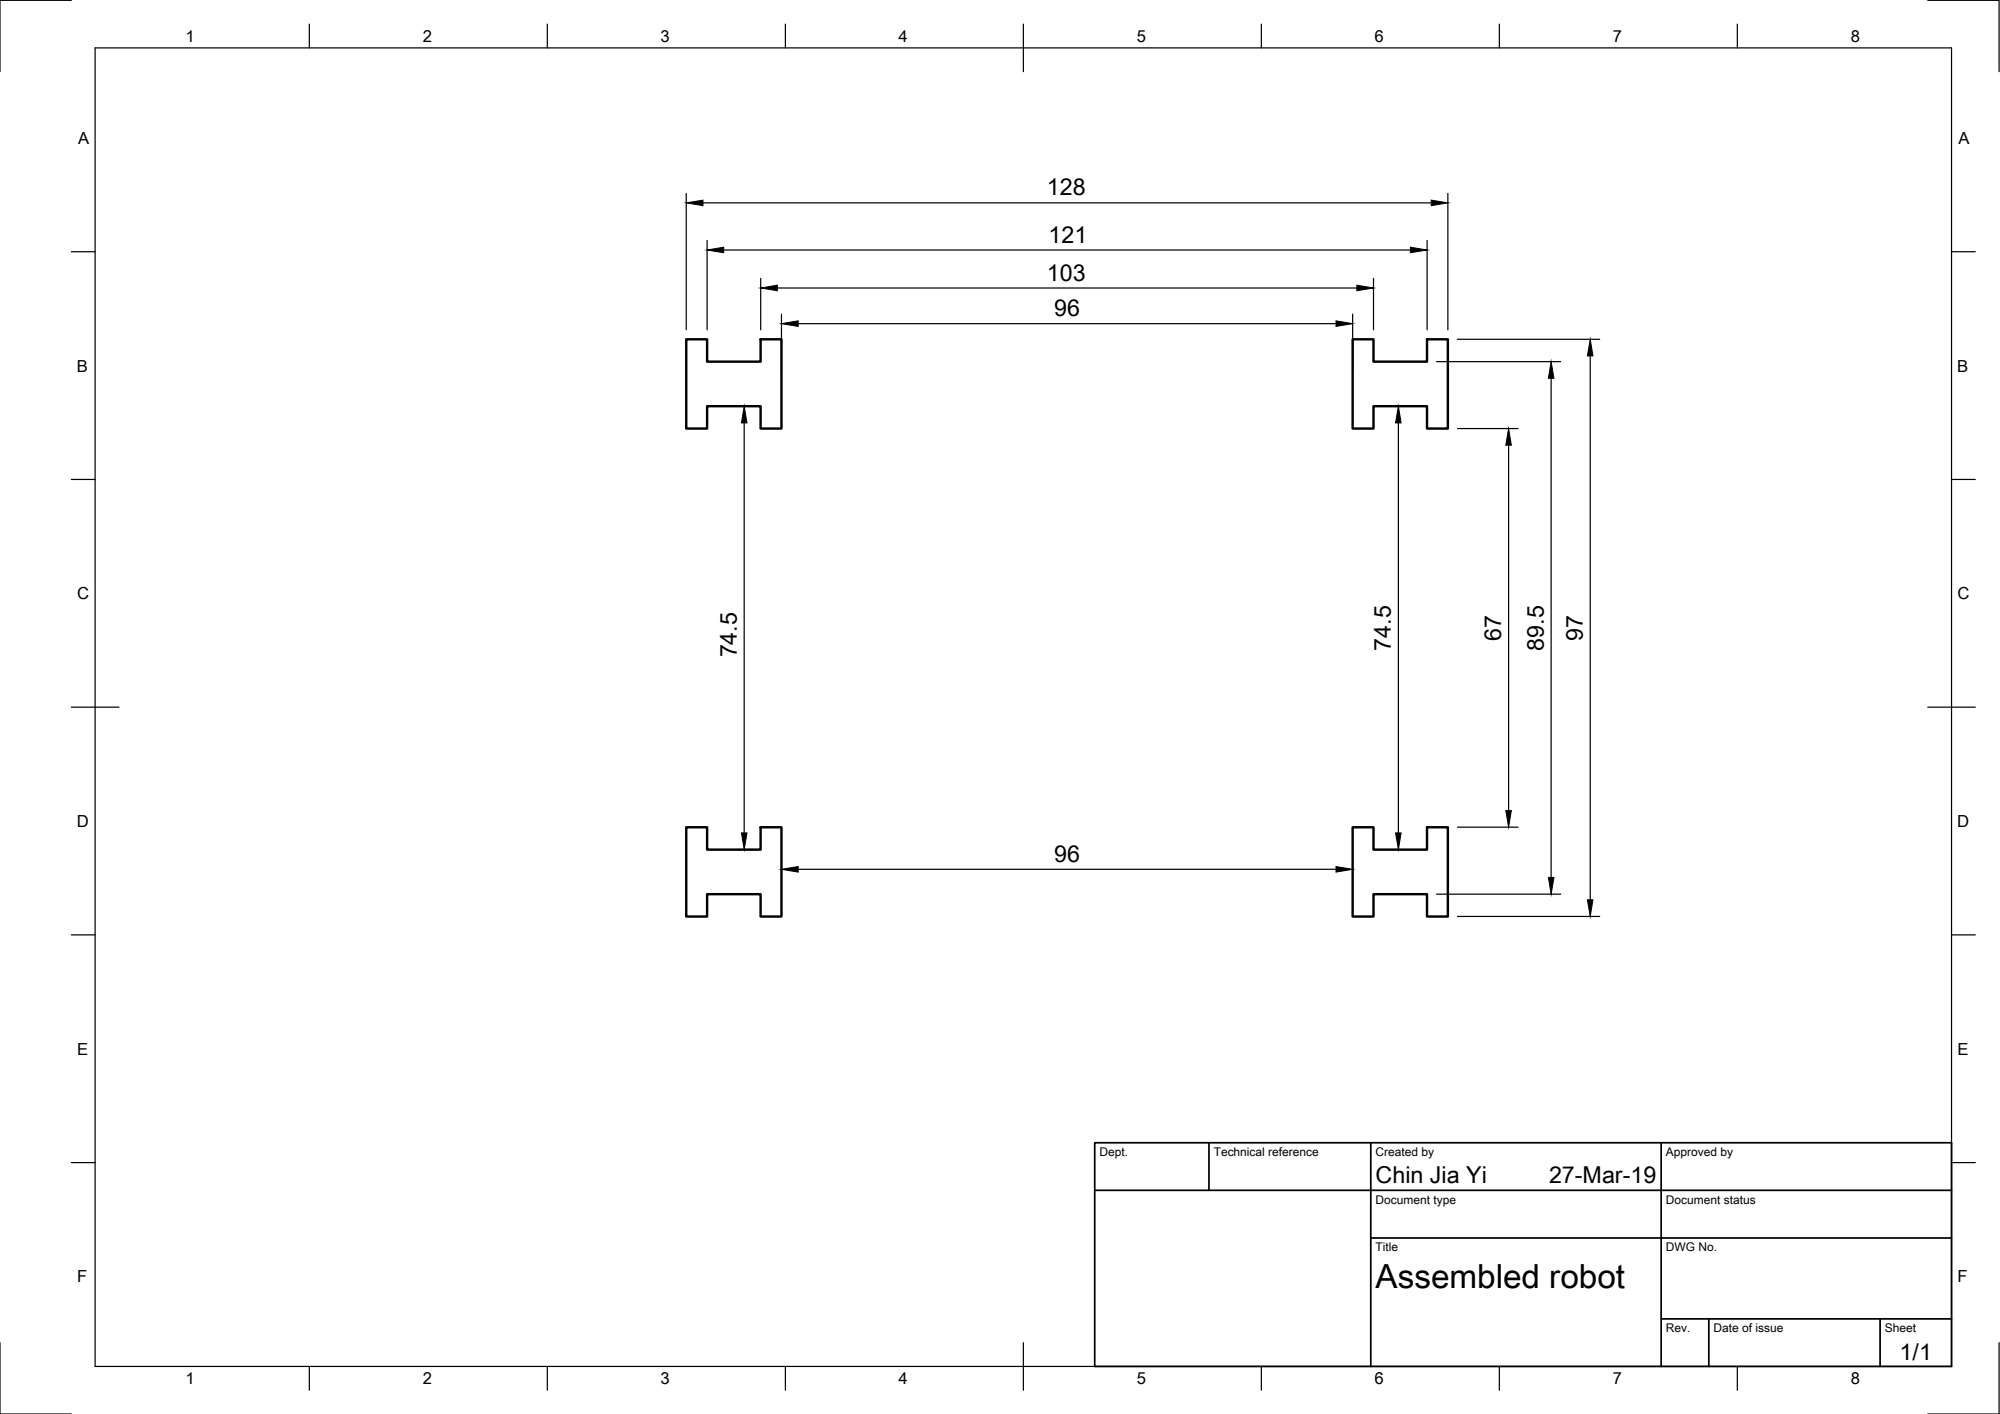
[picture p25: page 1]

Dept. | Technical reference | Created by Chin Jia Yi 27-Mar-19 | Approved by

Document type | Document status

Title Assembled robot | DWG No.

Rev. | Date of issue | Sheet 1/1

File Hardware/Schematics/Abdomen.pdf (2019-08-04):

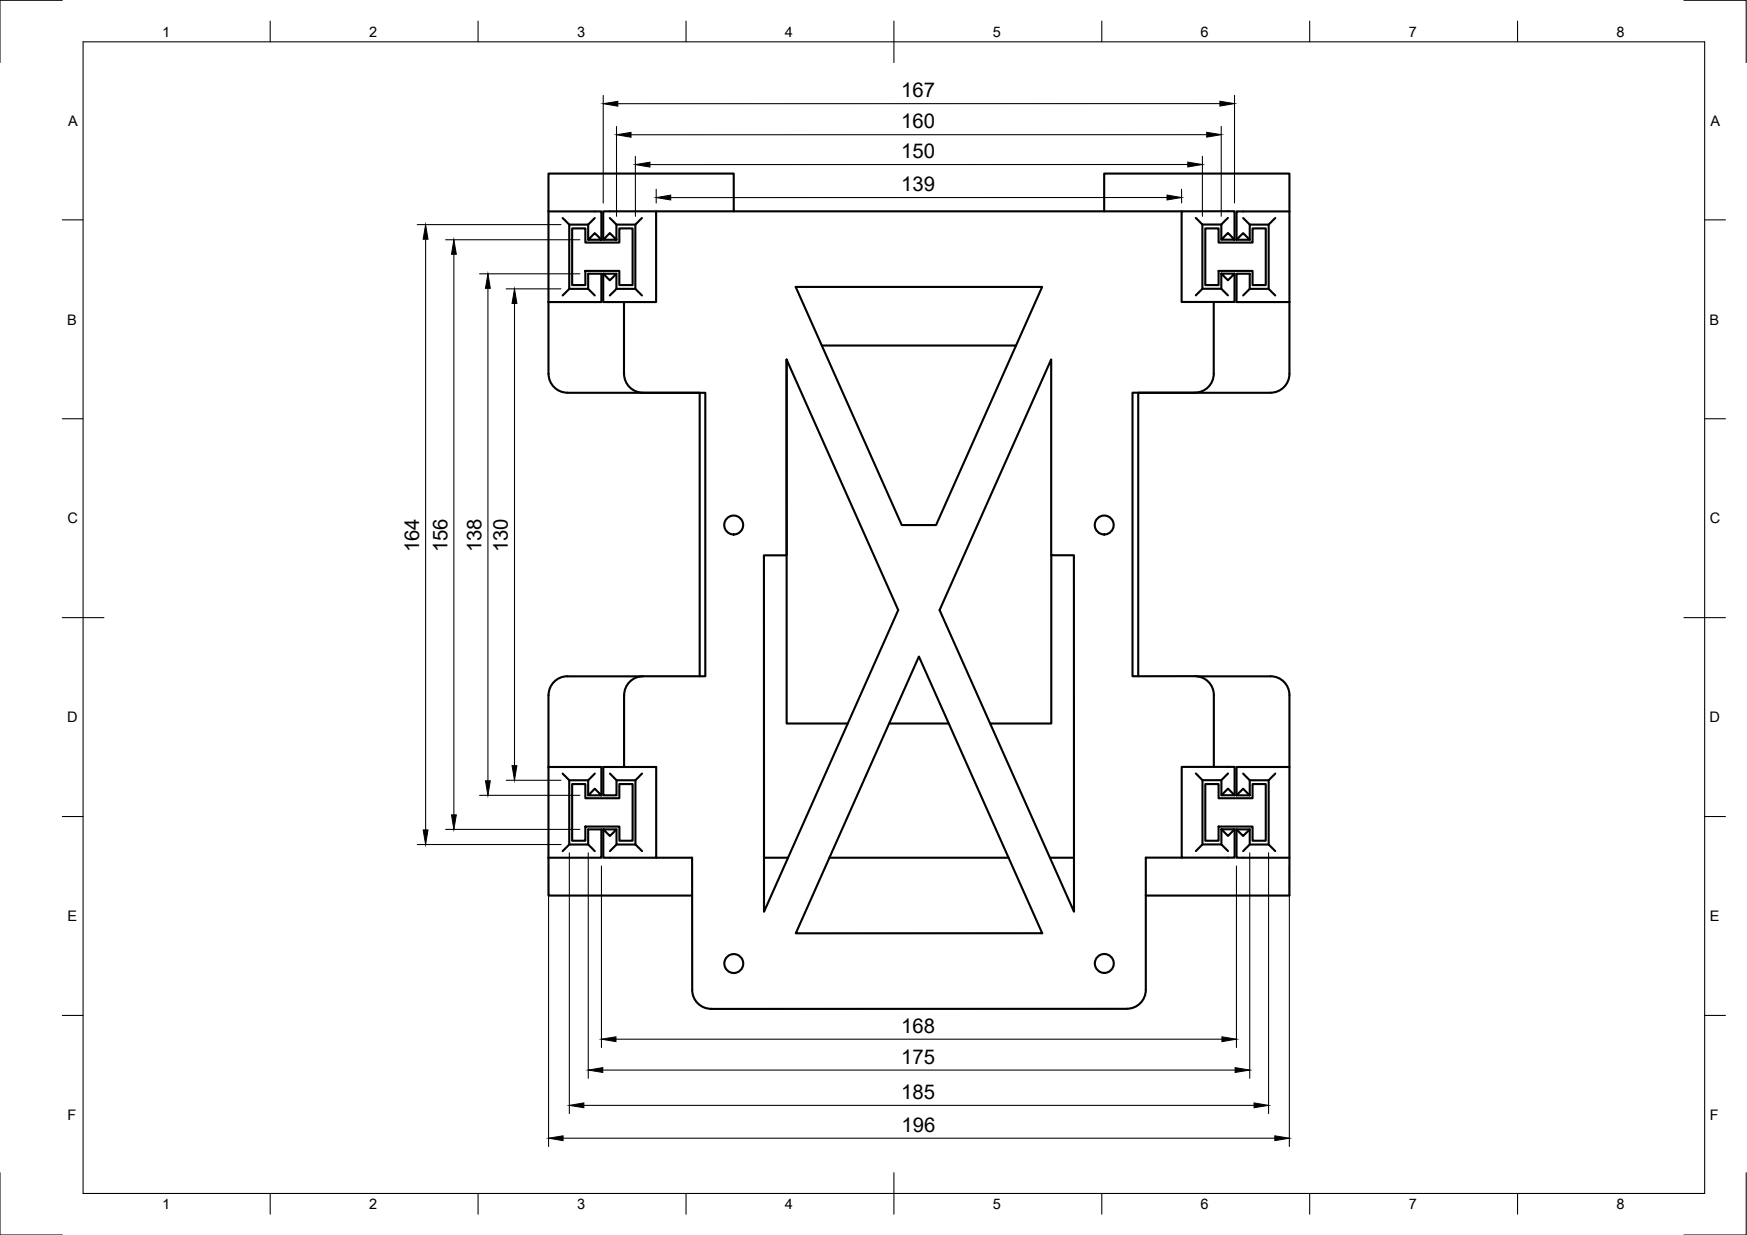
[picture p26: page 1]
8 BCDEF; ABCDEF

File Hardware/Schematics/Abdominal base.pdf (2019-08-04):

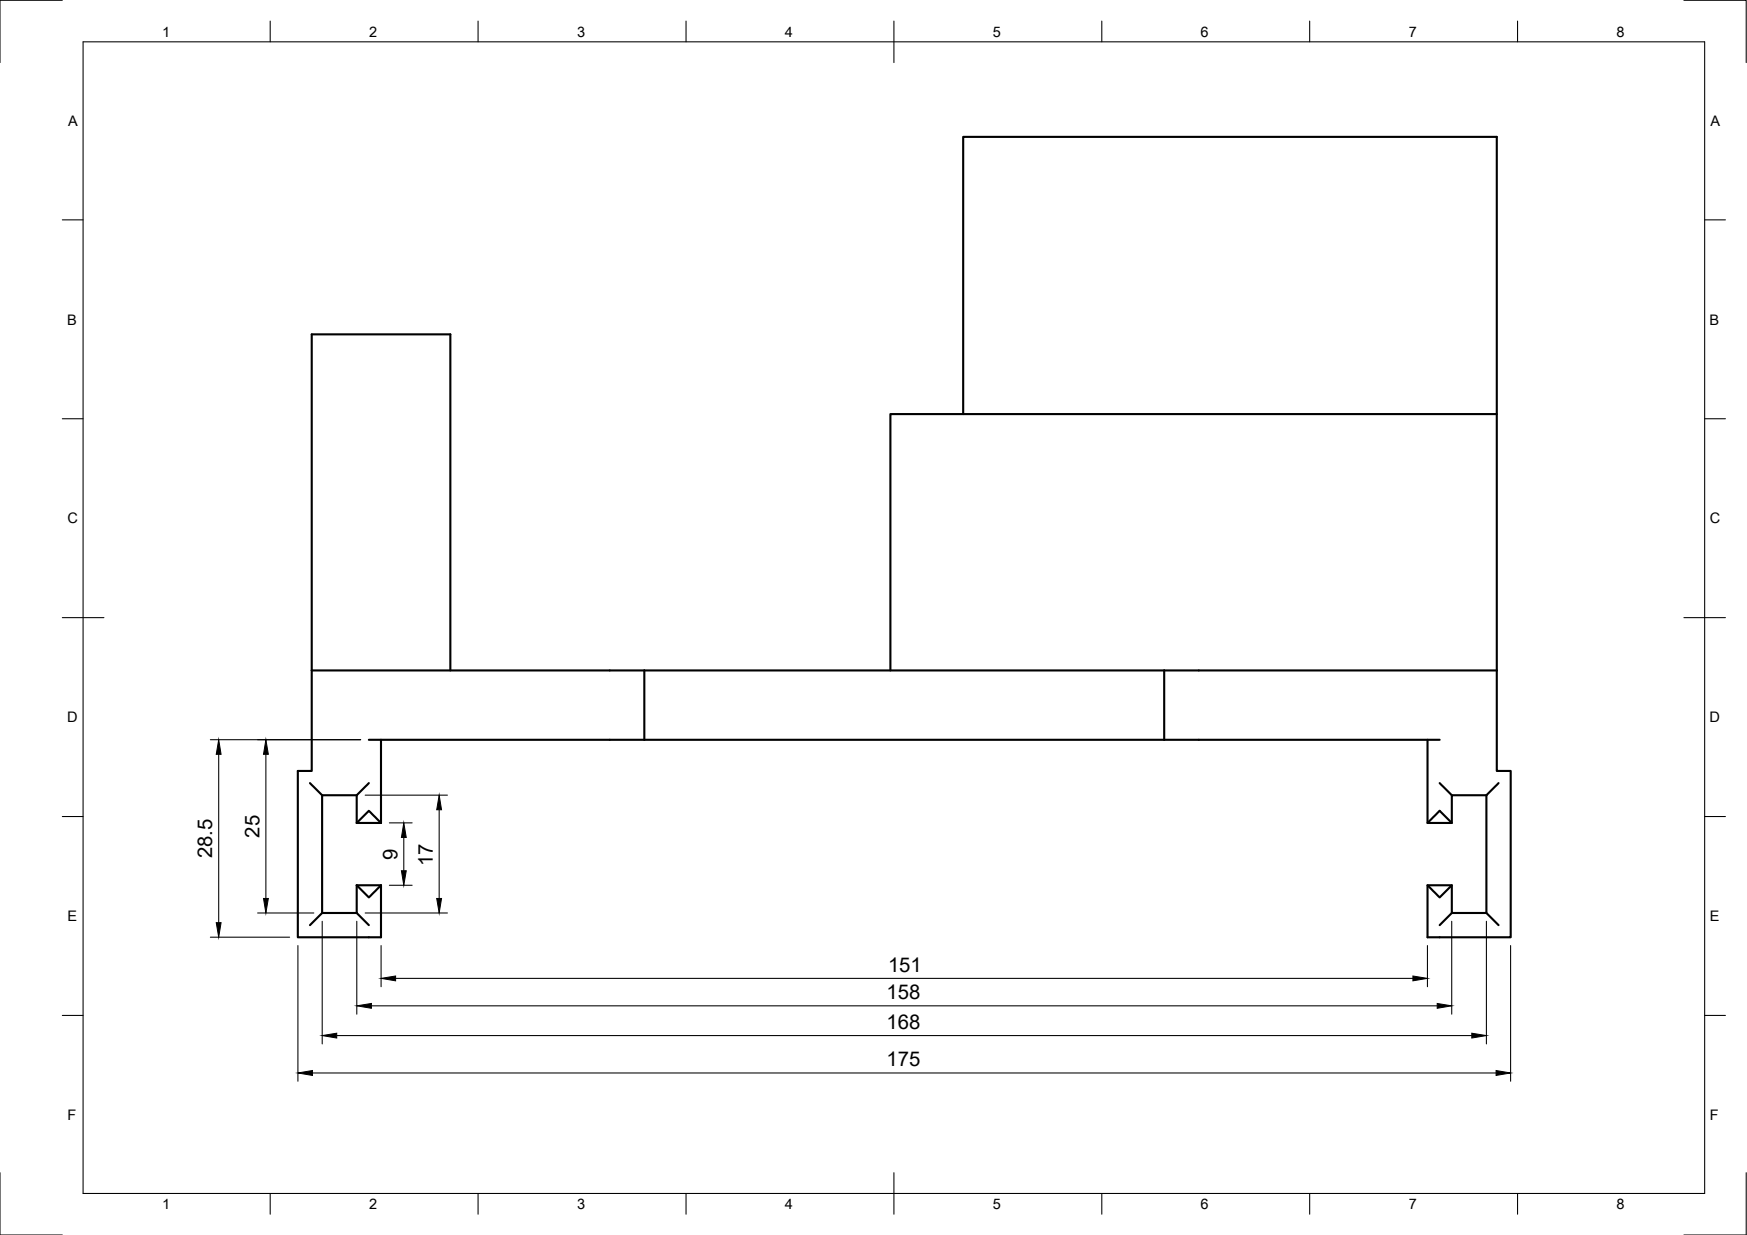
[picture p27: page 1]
8 BCDEF; ABCDEF

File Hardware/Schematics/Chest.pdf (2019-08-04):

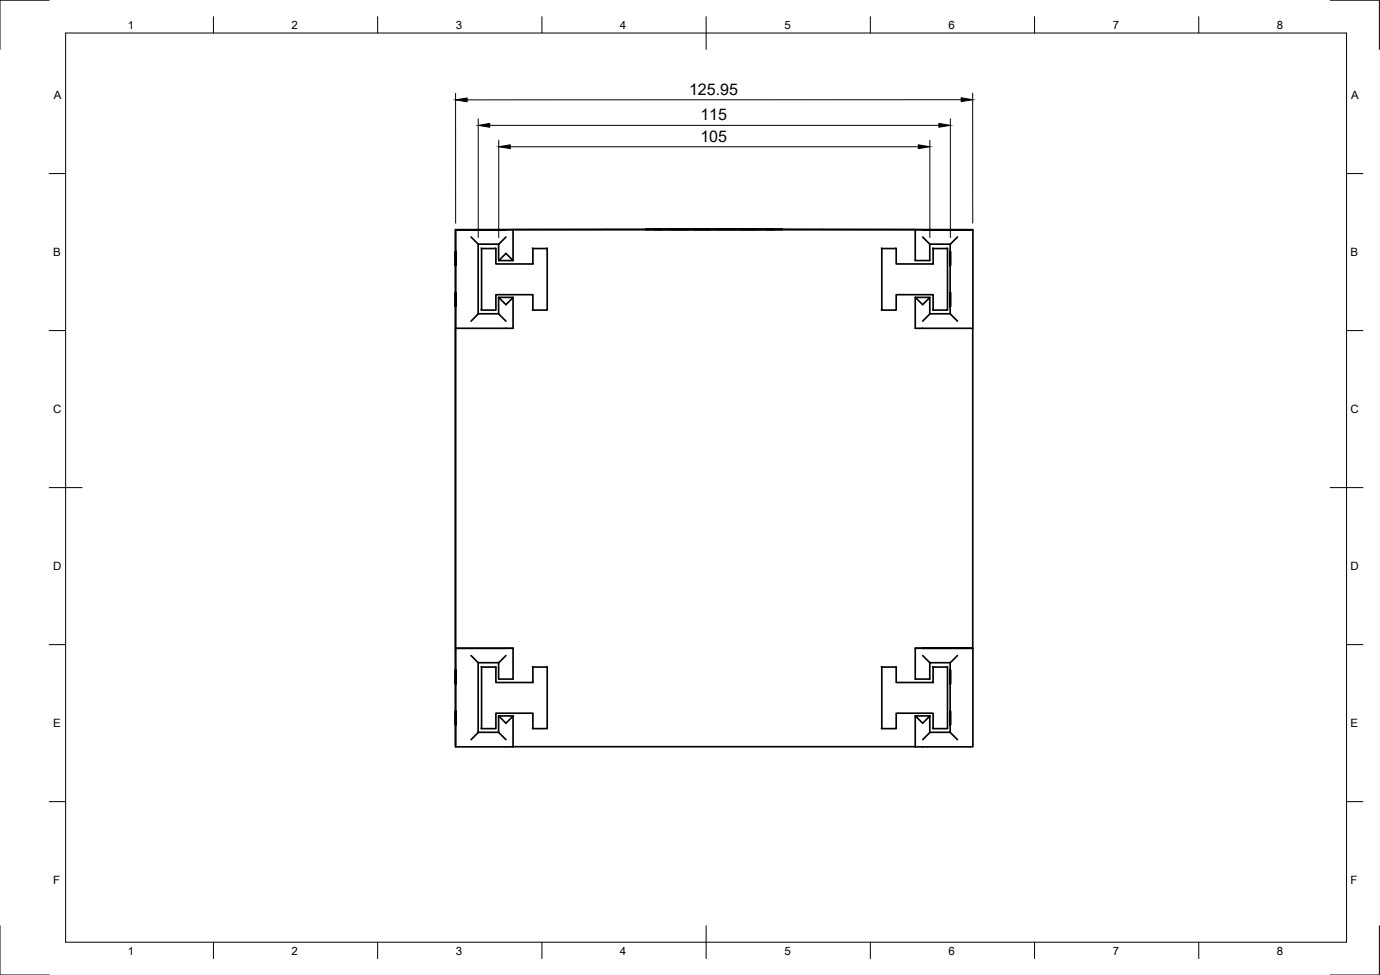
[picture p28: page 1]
8 BCDEF; ABCDEF

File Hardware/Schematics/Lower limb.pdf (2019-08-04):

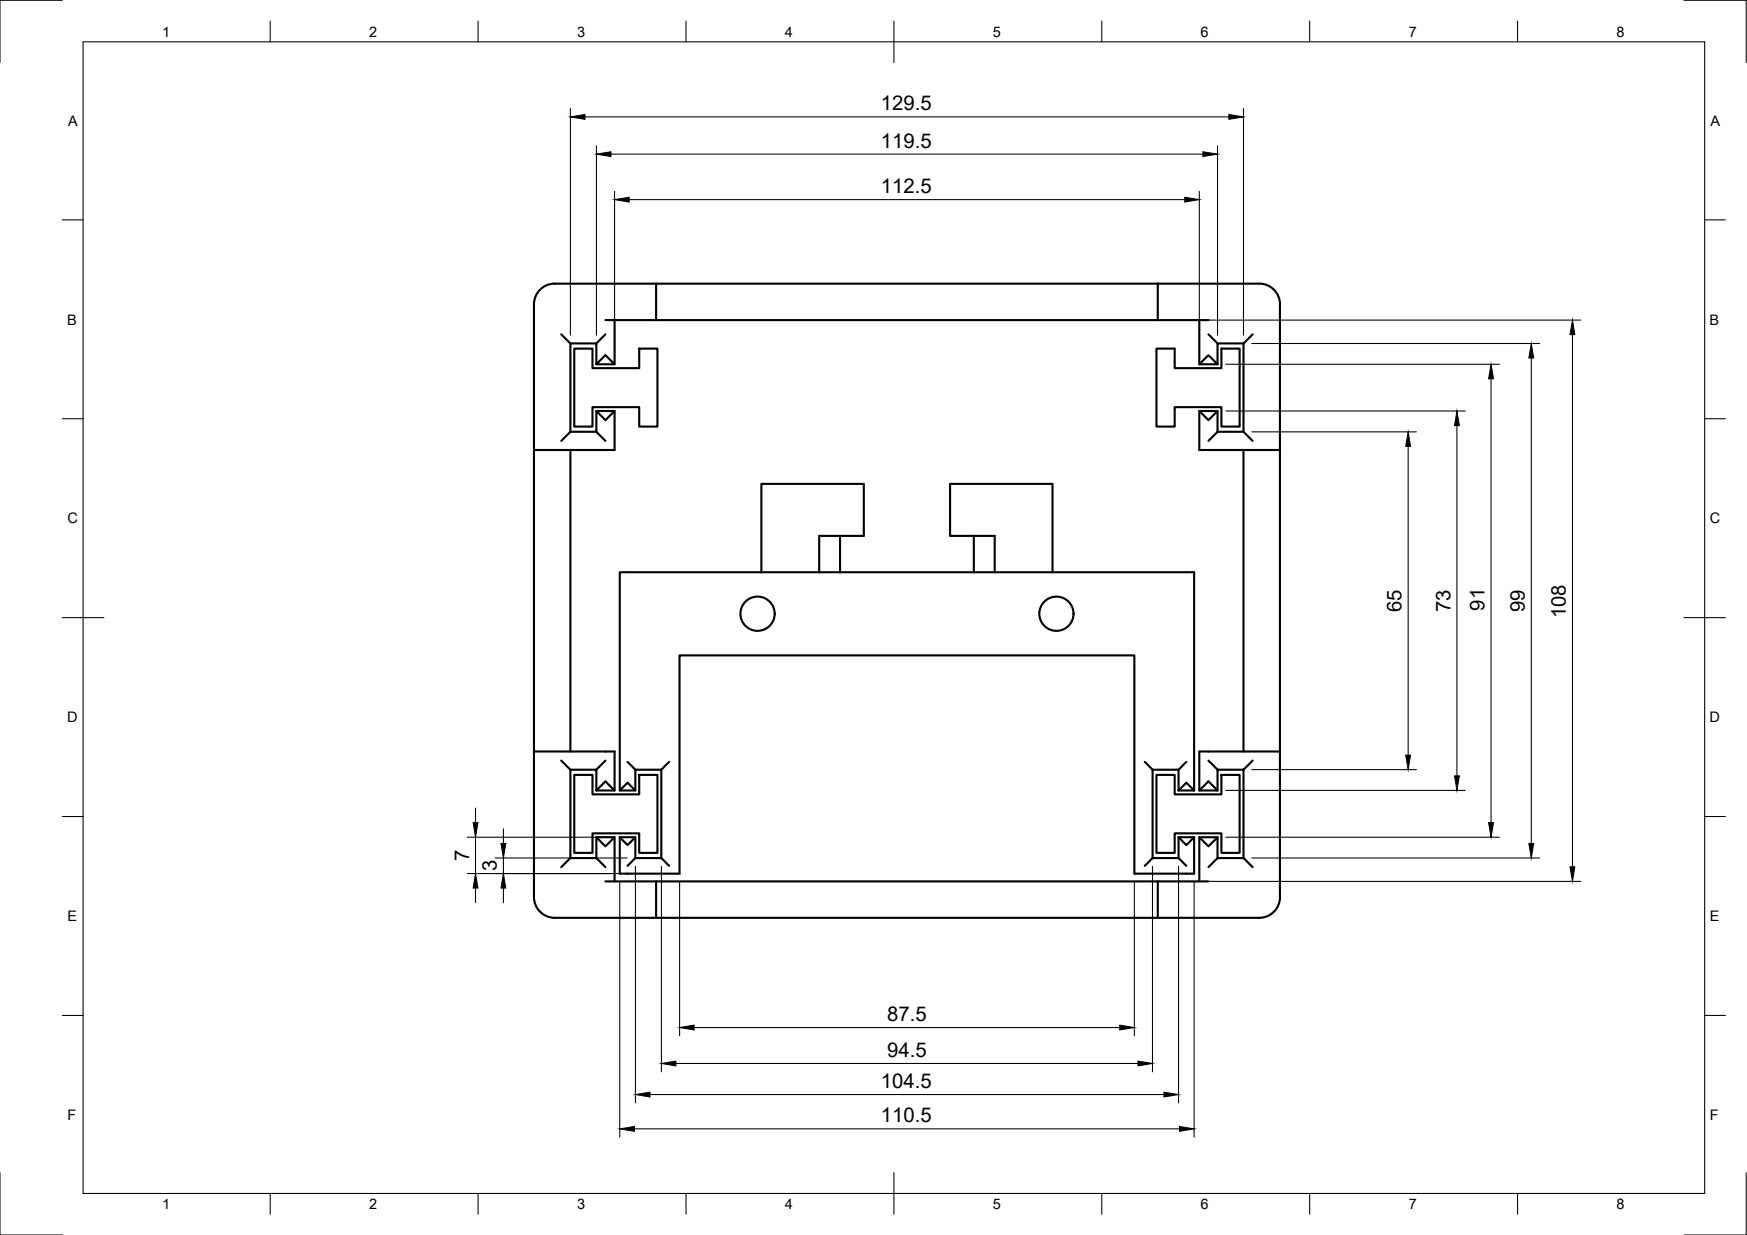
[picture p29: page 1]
8 BCDEF; ABCDEF

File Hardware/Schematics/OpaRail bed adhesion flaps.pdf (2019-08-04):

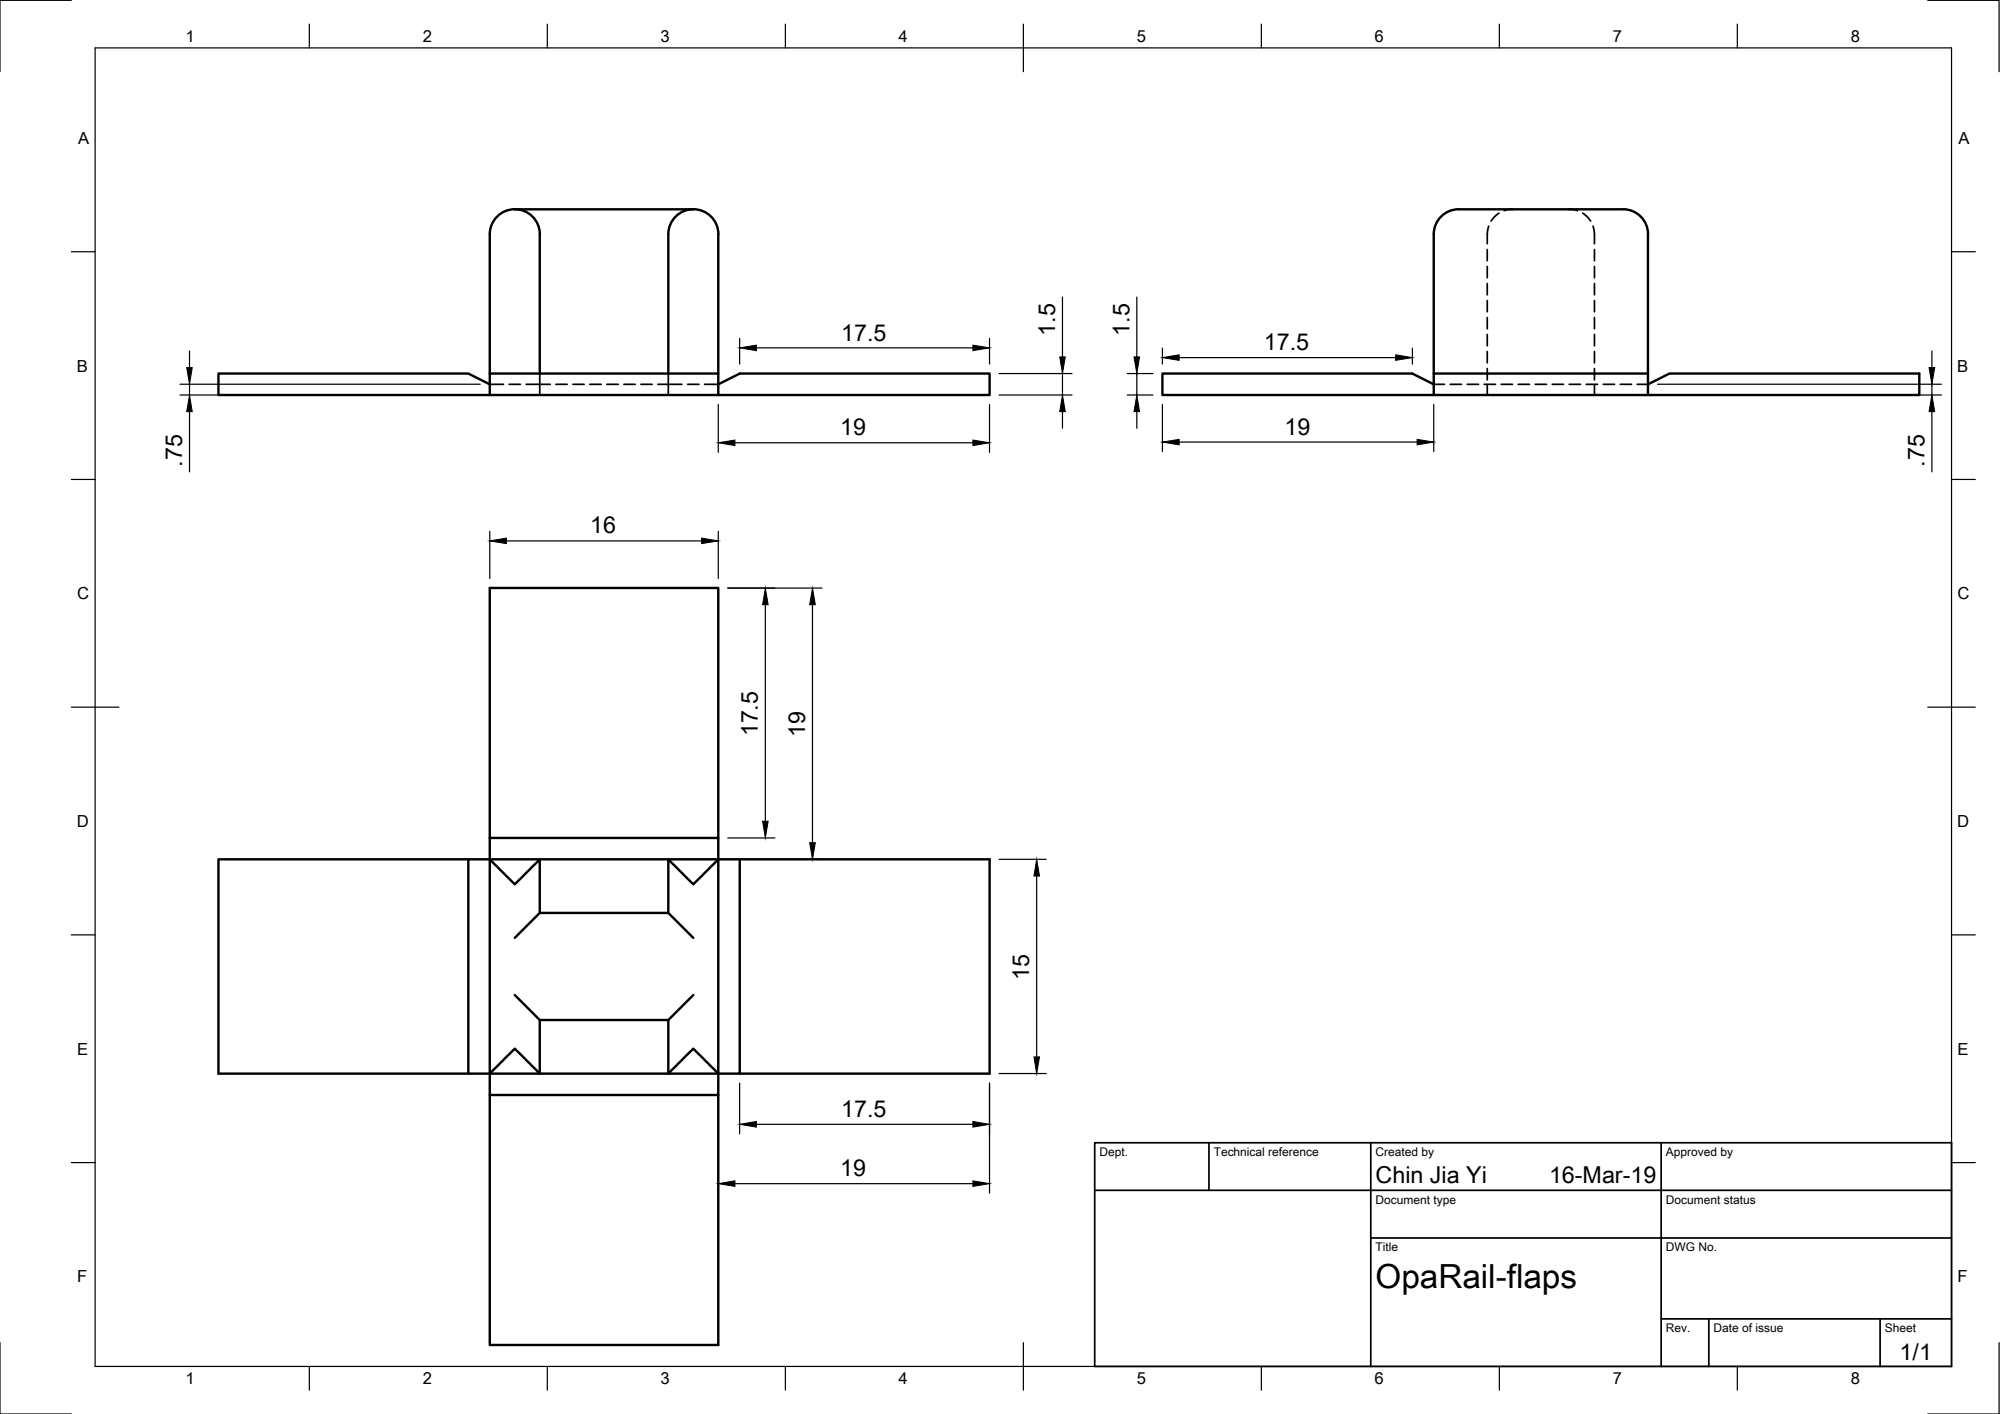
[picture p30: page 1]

Dept. | Technical reference | Created by Chin Jia Yi 16-Mar-19 | Approved by

Document type | Document status

Title OpaRail-flaps | DWG No.

Rev. | Date of issue | Sheet 1/1

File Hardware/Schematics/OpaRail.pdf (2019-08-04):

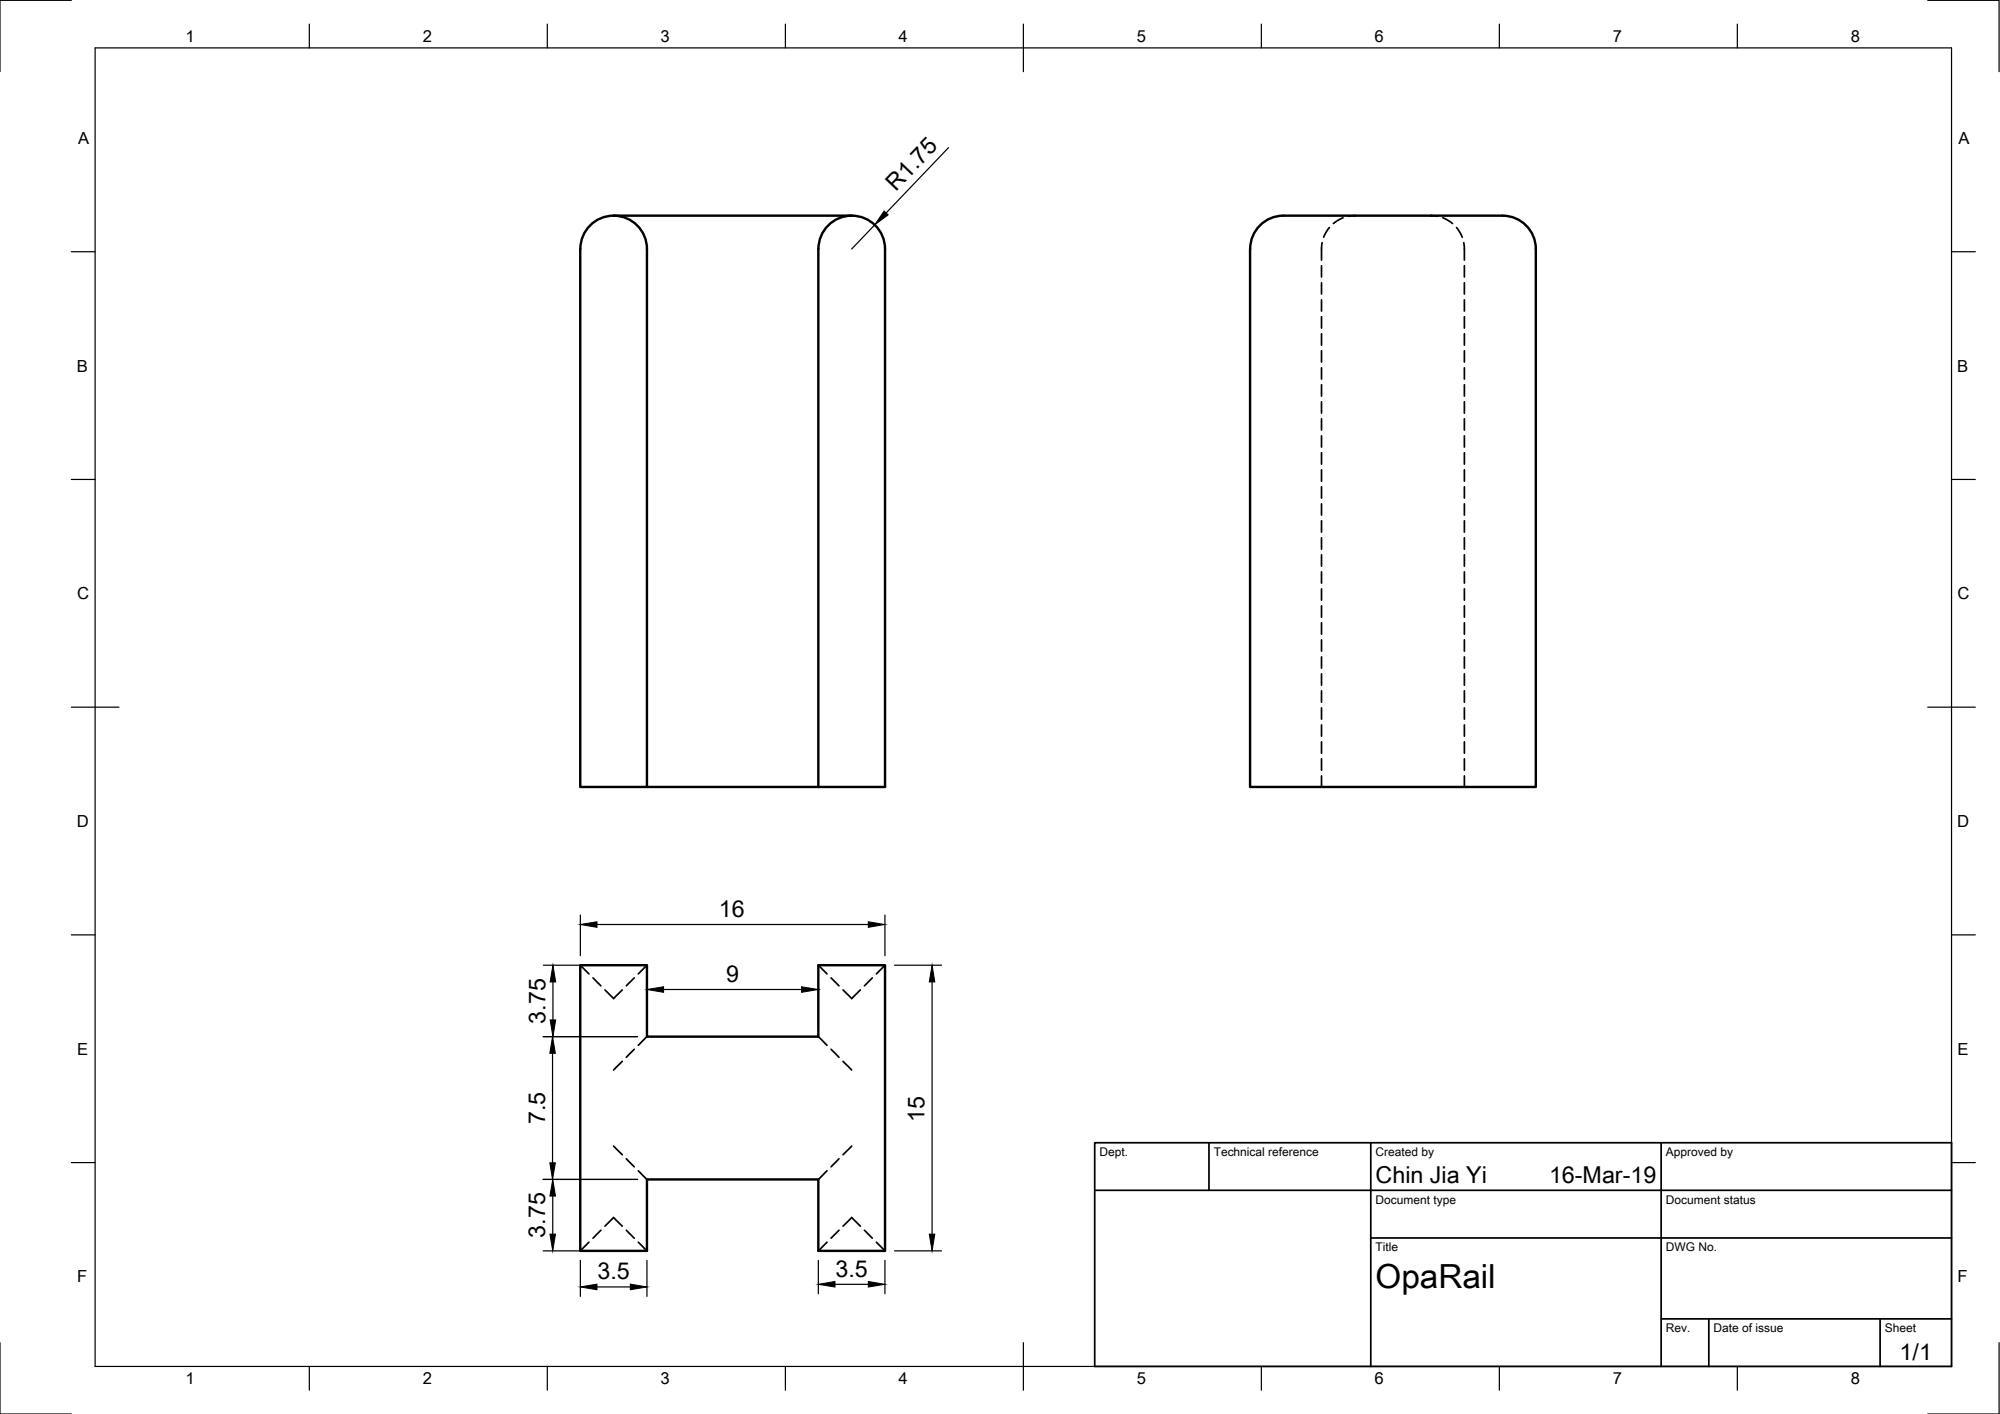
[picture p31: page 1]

Dept. | Technical reference | Created by Chin Jia Yi 16-Mar-19 | Approved by

Document type | Document status

Title OpaRail | DWG No.

Rev. | Date of issue | Sheet 1/1

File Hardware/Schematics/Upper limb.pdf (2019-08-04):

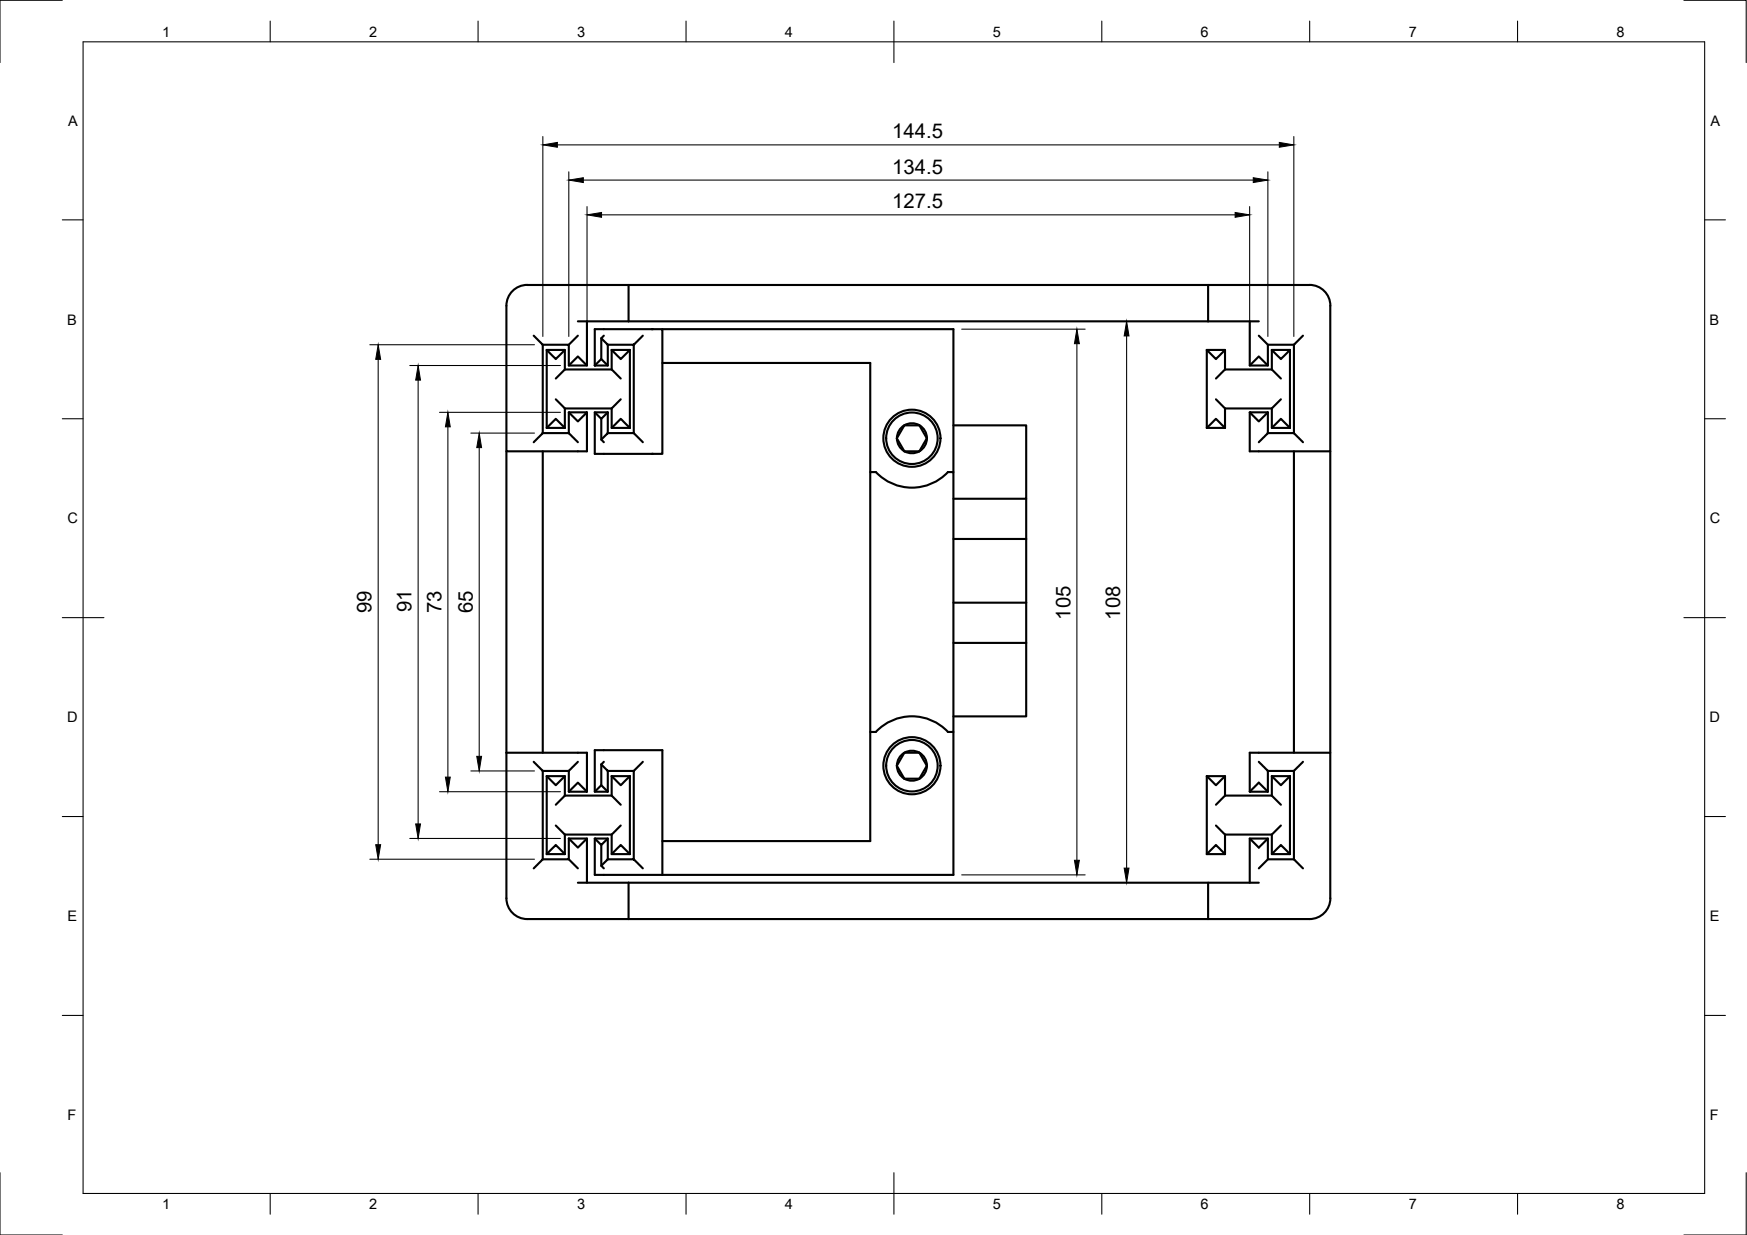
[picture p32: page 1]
8 BCDEF; ABCDEF 99

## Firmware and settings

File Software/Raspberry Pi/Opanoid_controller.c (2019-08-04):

#include <stdio.h>
#include <stdlib.h>
#include <pigpio.h>
 
int main(int argc, char *argv[])
{ 
   if (gpioInitialise() < 0)
   {
      fprintf(stderr, "pigpio initialisation failed\n");
      return 1;
   }
 
   /* Set GPIO modes */
   gpioServo(2, 1500); //leftThighX
   gpioServo(3, 1520); //leftThighZ
   gpioServo(4, 1510); //leftLegTwist
   gpioServo(14, 1420); //leftKnee
   gpioSetMode(22, PI_OUTPUT); //leftFootZ
   gpioSetMode(23, PI_OUTPUT); //leftFootX
   gpioSetMode(24, PI_OUTPUT); //leftToe
   gpioServo(15, 1515); //rightThighX
   gpioServo(17, 1500); //rightThighZ
   gpioServo(18, 1467); //rightLegTwist
   gpioSetMode(9, PI_OUTPUT); //rightToe
   gpioSetMode(10, PI_OUTPUT); //rightFootX
   gpioSetMode(25, PI_OUTPUT); //rightFootZ
 
   FILE *myFile;
   myFile = fopen("data_log_full_legs_walk.txt", "r");
   int i;
   int ch, character = 0, line = 0;
   
   /* Count number of values in log file */
   while ((ch = fgetc(myFile)) != EOF)
        {
            character++;
            if (ch == '\n')
                line++;
        }
        
   rewind(myFile); // Return to start of file to prepare for scanning
   
   /* Declare size of arrays based on number of values in log file */
   float numberArray0[1][line];
   float numberArray1[1][line];
   float numberArray2[1][line];
   float numberArray3[1][line];
   float numberArray4[1][line];
   float numberArray5[1][line];
   float numberArray6[1][line];
   float numberArray7[1][line];
   float numberArray8[1][line];
   float numberArray9[1][line];
   float numberArray10[1][line];
   float numberArray11[1][line];
   float numberArray12[1][line];
   float numberArray13[1][line];
   int leftThighX[line];
   int leftThighXRaw[line];
   int leftThighZ[line];
   int leftThighZRaw[line];   
   int leftLegTwist[line];
   int leftLegTwistRaw[line];   
   int leftKnee[line];
   int leftKneeRaw[line];   
   int rightThighX[line];
   int rightThighXRaw[line];   
   int rightThighZ[line];
   int rightThighZRaw[line];   
   int rightLegTwist[line];
   int rightLegTwistRaw[line];   
   int rightKnee[line];
   int rightKneeRaw[line];   
   int leftFootX[line];   
   int leftFootZ[line];   
   int leftToe[line];   
   int rightFootX[line];   
   int rightFootZ[line];   
   int rightToe[line];
   int leftThighXZero = 1455;
   int leftThighZZero = 1520;
   int leftLegTwistZero = 1510;
   int leftKneeZero = 1420;
   int rightThighXZero = 1515;
   int rightThighZZero = 1500;
   int rightLegTwistZero = 1467;
   int rightKneeZero = 1115;
   int leftFootXZero = 1530;
   int leftFootZZero = 1350;
   int leftToeZero = 1000;
   int rightFootXZero = 1500;
   int rightFootZZero = 1500;
   int rightToeZero = 1750;
   
   
   /* Scan values into numberArray */
   for (i = 0; i < line + 1; i++)
   {
       fscanf(myFile, "%f %f %f %f %f %f %f %f %f %f %f %f %f %f", &numberArray0[0][i], &numberArray1[0][i], &numberArray2[0][i], &numberArray3[0][i], &numberArray4[0][i], &numberArray5[0][i], &numberArray6[0][i], &numberArray7[0][i], &numberArray8[0][i], &numberArray9[0][i], &numberArray10[0][i], &numberArray11[0][i], &numberArray12[0][i], &numberArray13[0][i]);
       /* Convert values into usable range for servo and put into finalArray */
       leftThighXRaw[i] = ((numberArray0[0][i]/140) * 950) + leftThighXZero;
       leftThighX[i] = (leftThighXRaw[i] + leftThighXRaw[i - 1] + leftThighXRaw[i - 2] + leftThighXRaw[i - 3])/4;
       if(leftThighX[i] > (leftThighXZero + 210)) {
		   leftThighX[i] = leftThighXZero + 210;
	   }
       else if(leftThighX[i] < leftThighXZero) {
		   leftThighX[i] = leftThighXZero;
	   }
	   
       leftThighZRaw[i] = -((numberArray1[0][i]/90) * 950) + leftThighZZero;
       leftThighZ[i] = (leftThighZRaw[i] + leftThighZRaw[i - 1] + leftThighZRaw[i - 2] + leftThighZRaw[i - 3])/4;
       if(leftThighZ[i] > (leftThighZZero + 700)) {
		   leftThighZ[i] = leftThighZZero + 700;
	   }
       else if(leftThighZ[i] < (leftThighZZero - 700)) {
		   leftThighZ[i] = leftThighZZero - 700;
	   }
       
	   leftLegTwistRaw[i] = ((numberArray2[0][i]/90) * 950) + leftLegTwistZero;
	   leftLegTwist[i] = (leftLegTwistRaw[i] + leftLegTwistRaw[i - 1] + leftLegTwistRaw[i - 2] + leftLegTwistRaw[i - 3])/4;
	   if(leftLegTwist[i] > (leftLegTwistZero + 100)) {
		   leftLegTwist[i] = leftLegTwistZero + 100;
	   }
       else if(leftLegTwist[i] < (leftLegTwistZero - 400)) {
		   leftLegTwist[i] = leftLegTwistZero - 400;
	   }
	   
	   leftKneeRaw[i] = ((numberArray3[0][i]/90) * 950) + leftKneeZero;
	   leftKnee[i] = (leftKneeRaw[i] + leftKneeRaw[i - 1] + leftKneeRaw[i - 2] + leftKneeRaw[i - 3])/4;
	   if(leftKnee[i] > (leftKneeZero + 1000)) {
		   leftKnee[i] = leftKneeZero + 1000;
	   }
       else if(leftKnee[i] < leftKneeZero) {
		   leftKnee[i] = leftKneeZero;
	   }
	   
	   rightThighXRaw[i] = -((numberArray4[0][i]/140) * 950) + rightThighXZero;
	   rightThighX[i] = (rightThighXRaw[i] + rightThighXRaw[i - 1] + rightThighXRaw[i - 2] + rightThighXRaw[i - 3])/4;
	   if(rightThighX[i] > rightThighXZero) {
		   rightThighX[i] = rightThighXZero;
	   }
       else if(rightThighX[i] < (rightThighXZero - 210)) {
		   rightThighX[i] = rightThighXZero - 210;
	   }
	   
	   rightThighZRaw[i] = ((numberArray5[0][i]/90) * 950) + rightThighZZero;
	   rightThighZ[i] = (rightThighZRaw[i] + rightThighZRaw[i - 1] + rightThighZRaw[i - 2] + rightThighZRaw[i - 3])/4;
	   if(rightThighZ[i] > (rightThighZZero + 700)) {
		   rightThighZ[i] = rightThighZZero + 700;
	   }
       else if(rightThighZ[i] < (rightThighZZero - 700)) {
		   rightThighZ[i] = rightThighZZero - 700;
	   }
	   
	   rightLegTwistRaw[i] = -((numberArray6[0][i]/90) * 950) + rightLegTwistZero;
	   rightLegTwist[i] = (rightLegTwistRaw[i] + rightLegTwistRaw[i - 1] + rightLegTwistRaw[i - 2] + rightLegTwistRaw[i - 3])/4;
	   if(rightLegTwist[i] > (rightLegTwistZero + 400)) {
		   rightLegTwist[i] = rightLegTwistZero + 400;
	   }
       else if(rightLegTwist[i] < (rightLegTwistZero - 100)) {
		   rightLegTwist[i] = rightLegTwistZero - 100;
	   }
	   
	   rightKneeRaw[i] = -((numberArray7[0][i]/90) * 950) + rightKneeZero;
	   rightKnee[i] = (rightKneeRaw[i] + rightKneeRaw[i - 1] + rightKneeRaw[i - 2] + rightKneeRaw[i - 3])/4;
	   if(rightKnee[i] > rightKneeZero) {
		   rightKnee[i] = rightKneeZero;
	   }
       else if(rightKnee[i] < (rightKneeZero - 1000)) {
		   rightKnee[i] = rightKneeZero - 1000;
	   }
	   
	   leftFootX[i] = -((numberArray8[0][i]/90) * 950) + leftFootXZero;
	   if(leftFootX[i] > (leftFootXZero + 140)) {
		   leftFootX[i] = leftFootXZero + 140;
	   }
	   else if(leftFootX[i] < (leftFootXZero - 160)) {
		   leftFootX[i] = leftFootXZero - 160;
	   }
	   
	   leftFootZ[i] = -((numberArray9[0][i]/140) * 950) + leftFootZZero;
	   if(leftFootZ[i] > (leftFootZZero + 400)) {
		   leftFootZ[i] = leftFootZZero + 400;
	   }
	   else if(leftFootZ[i] < (leftFootZZero - 180)) {
		   leftFootZ[i] = leftFootZZero - 180;
	   }
	   
	   leftToe[i] = ((numberArray10[0][i]/90) * 950) + leftToeZero;
	   if(leftToe[i] > (leftToeZero + 700)) {
		   leftToe[i] = leftToeZero + 700;
	   }
	   else if(leftToe[i] < (leftToeZero - 130)) {
		   leftToe[i] = leftToeZero - 130;
	   }
	   
	   rightFootX[i] = -((numberArray11[0][i]/90) * 950) + rightFootXZero;
	   if(rightFootX[i] > (rightFootXZero + 300)) {
		   rightFootX[i] = rightFootXZero + 300;
	   }
	   else if(rightFootX[i] < (rightFootXZero - 170)) {
		   rightFootX[i] = rightFootXZero - 170;
	   }	   
	   
	   rightFootZ[i] = ((numberArray12[0][i]/140) * 950) + rightFootZZero;
	   if(rightFootZ[i] > (rightFootZZero + 80)) {
		   rightFootZ[i] = rightFootZZero + 80;
	   }
	   else if(rightFootZ[i] < (rightFootZZero - 190)) {
		   rightFootZ[i] = rightFootZZero - 190;
	   }	
	   
	   rightToe[i] = -((numberArray13[0][i]/90) * 950) + rightToeZero;
	   if(rightToe[i] > (rightToeZero + 350)) {
		   rightToe[i] = rightToeZero + 350;
	   }
	   else if(rightToe[i] < (rightToeZero - 750)) {
		   rightToe[i] = rightToeZero - 750;
	   }	
   }	    
   /* Move servo based on values in finalArray */
   for (i = 0; i < line + 1; i = i + 25)
   {	  
	    gpioServo(2, leftThighX[i]);
	    gpioServo(3, leftThighZ[i]);
	    //gpioServo(4, leftLegTwist[i]);
	    gpioServo(14, leftKnee[i]);
	    gpioServo(15, rightThighX[i]);
	    gpioServo(17, rightThighZ[i]);
	    //gpioServo(18, rightLegTwist[i]);
	    gpioServo(27, rightKnee[i]);
	    gpioServo(22, leftFootZ[i]);
	    gpioServo(23, leftFootX[i]);
	    gpioServo(24, leftToe[i]);
	    gpioServo(9, rightToe[i]);
	    gpioServo(10, rightFootX[i]);
	    gpioServo(25, rightFootZ[i]);
	    printf("%f %f %f %f %f %f %f \n", numberArray7[0][i], numberArray8[0][i], numberArray9[0][i], numberArray10[0][i], numberArray11[0][i], numberArray12[0][i], numberArray13[0][i]);
	    time_sleep(0.03;	
   }
   
	
   /* Stop DMA, release resources */
   gpioTerminate();
 
   return 0;
}

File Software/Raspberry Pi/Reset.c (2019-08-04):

#include <stdio.h>
 
#include <pigpio.h>
 
int main(int argc, char *argv[])
{ 
	if (gpioInitialise() < 0)
	{
	  fprintf(stderr, "pigpio initialisation failed\n");
	  return 1;
	}
    
    /* Set GPIO modes */
    gpioSetMode(2, PI_OUTPUT);
    gpioSetMode(3, PI_OUTPUT);
    gpioSetMode(4, PI_OUTPUT); 
    gpioSetMode(9, PI_OUTPUT); 
    gpioSetMode(10, PI_OUTPUT); 
    gpioSetMode(14, PI_OUTPUT); 
    gpioSetMode(15, PI_OUTPUT); 
    gpioSetMode(17, PI_OUTPUT); 
    gpioSetMode(18, PI_OUTPUT); 
    gpioSetMode(22, PI_OUTPUT); 
    gpioSetMode(23, PI_OUTPUT); 
    gpioSetMode(24, PI_OUTPUT);       gpioSetMode(23, PI_OUTPUT); 

    gpioSetMode(27, PI_OUTPUT);

	gpioServo(2, 1500); //leftThighX
	gpioServo(3, 1520); //leftThighZ
	gpioServo(4, 1510); //leftLegTwist
	gpioServo(9, 1750); //rightToe
	gpioServo(10, 1500); //rightFootX
	gpioServo(14, 1420); //leftKnee
	gpioServo(15, 1515); //rightThighX
	gpioServo(17, 1500); //rightThighZ
	gpioServo(18, 1467); //rightLegTwist
	gpioServo(22, 1350); //leftFootZ
	gpioServo(23, 1530); //leftFootX
	gpioServo(24, 1000); //leftToe
	gpioServo(25, 1500); //rightFootZ
	gpioServo(27, 1115); //rightKnee
	
	time_sleep(0.4);
 
	/* Stop DMA, release resources */
	gpioTerminate();

	return 0;
}

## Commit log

2019-07-04 added ROS package and updated software doc
    [09-publishjoints.urdf.xacro, 10-firsttransmission.urdf.xacro, 11-limittransmission.urdf.xacro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]
2019-08-02 updated stl files
    [Arm attachment point.stl, Left pelvis attachment bracket.stl, Right pelvis attachment bracket.stl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]
2019-08-03 removed unnecessary files
    [09-publishjoints.urdf.xacro, 10-firsttransmission.urdf.xacro, 11-limittransmission.urdf.xacro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]
2019-08-03 updated files
    [opanoid_full.urdf, opanoid_full_2.urdf]
2019-08-03 streamlined project opanoid package
    [opanoid_full.urdf, opanoid_full_2.urdf, opanoid_sketch.urdf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]
2019-08-04 added print settings
2019-08-04 updated schematics
2019-11-17 added image to readme
    [Arm attachment point.stl]
